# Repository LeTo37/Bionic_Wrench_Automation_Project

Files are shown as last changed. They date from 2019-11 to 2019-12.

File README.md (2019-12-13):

# Part_Placement_Automation_Project
This repository contains the details of my final project for my Masters in Robotics at Northwestern Univeristy. This project entailed the automation of a part of the production process for a specific Wrench and was supervised by Professor Dan Brown.

## Overview
The initial goal of this project was to observe the manufacturing process of the wrench and identify a bottleneck in the process that can be addressed by automation. With that goal set out, there were no set requirements on what should be automated and how it should be automated. This allowed for freedom and trust in following the design process to achieve the optimal solution to this problem.

After journey mapping the manufacturing process, giving time values for each task as well as automatibility ratings and assessments regarding what would be gained from automation, it was clear to see that the set of tasks involved in placing the wrench jaws in the wrench are both the most automatable and automating them will result in the most gain to the entire process. As such the task was set out to use/design whatever is deemed appropriate to automate this process in a way that is both accurate and fast.

The result is shown in the video below:
Mario Kart (https://www.youtube-nocookie.com/embed/1hQX_BQMhLg "Mario Kart")

As will be detailed, the mechanical design for this project was primarily done using <a href="https://www.onshape.com/" target="_blank">OnShape</a> CAD software, the construction of the rig was done using various prototyping methods such as 3D printing and Laser Cutting, a PIC32MX795F512H microcontroller was used to control the system and the relevant peripheral circuitry and coding of the microcontroller was done in C. 

## Approach
As mentioned above, the first step of this project was just to observe. Professor Brown gave me videos of the current production process for the wrench and I began to make note of each task being undertaken, how long each task was taking and how that task affects the other tasks. It was clear that the biggest bottleneck in the process was the placing of the wrench jaws in the wrench. This task represented the biggest gain from automation but also perhaps one of the most challenging steps to automate given the precise needs for placing the jaw as well as the small amount of space in the middle of the wrench in which a mechanism can actuate.

So begun the iterative process of design. The bulk of work done in this project was in mechanical design, each week brought about a new iteration of the current design as well as thoughts on a new approach. That journey can be mapped by following the different "STL" files of the various designs that were cycled through before arriving at the final stop. 

It became important to create journey maps of best case scenarios, so as to assess the approach and figure out what could be done in time as well as what could be done better.
<!-- ![Wrench_Journey_Map](media/Wrench_Journey_Map.pdf) -->
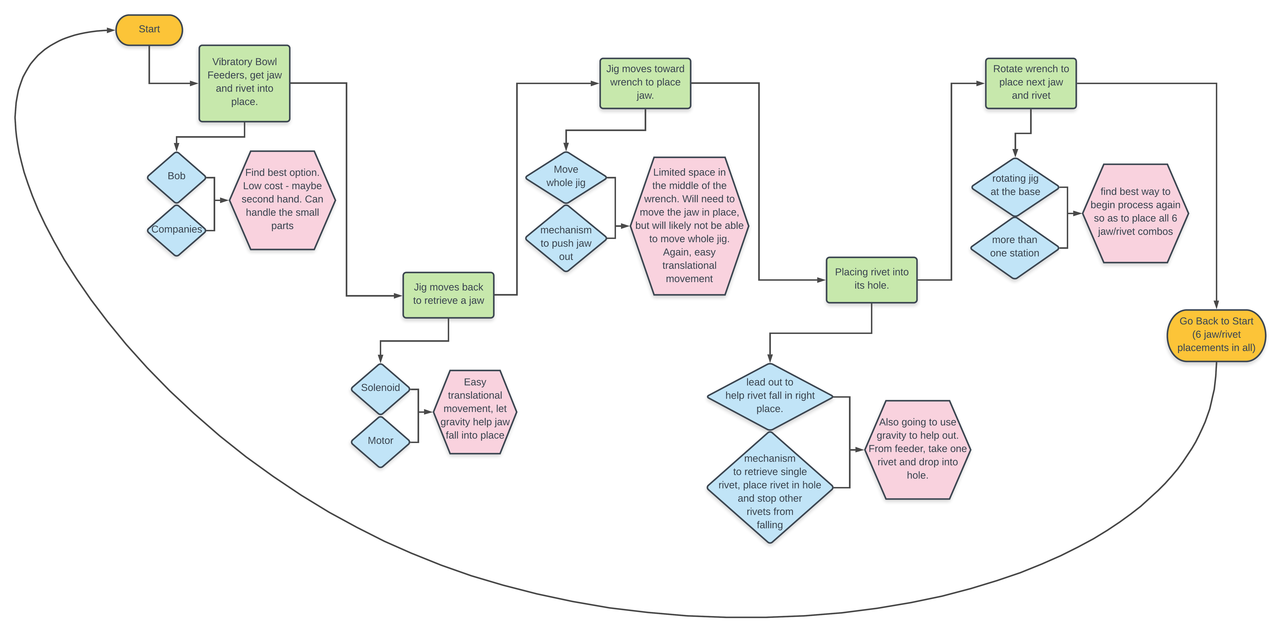
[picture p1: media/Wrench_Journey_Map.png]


A big change in the approach came about when it was decided that using gravity to place the jaws could simplify the process by eliminating the need to actuate within the small space in the middle of the wrench. This came about as a serendipitous thought during a brainstorming session with Professor Brown. 
As such, the final approach was to use gravity to place the jaws in the wrench, with the assistance of an electromagnet and to rotate the wrench around the jig and repeat - so as to place all 6 jaws. This is further detailed in the READMEs of each directory.

## Mechanical Design
The mechanical design involved in this project was by far the most important, most complex and thus the most time consuming aspect of the project. As is the nature of design, it involved a lot of iterations as well as a few changes in approach that ultimately led to the final design. This final set up is shown below.

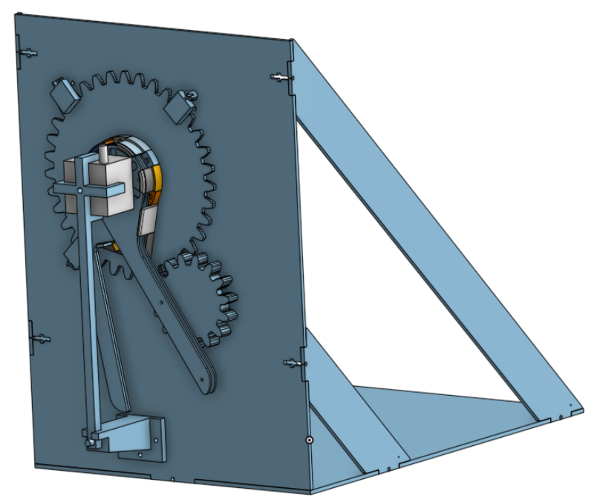
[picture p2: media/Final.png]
Final


The design process is discussed further in the [Mechanical Design Directory](/Mechanical_Design).

## Electronics

[This](/Electronics) directory contains the <a href="https://www.autodesk.com/products/eagle/overview" target="_blank">EAGLE CAD</a> files used to develop the schematics of the circuitry used in this project. It further contains a README explaining the circuitry used.

## Code

The C code used to program the microcontroller is in [this](/Code). directory.

<!-- ## Future Work -->

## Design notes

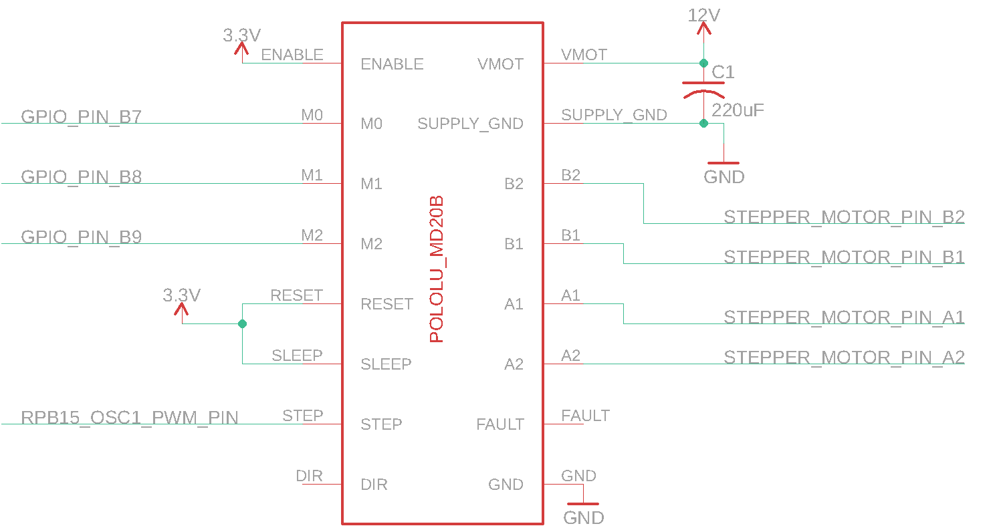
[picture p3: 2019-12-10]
Electronics/STEPPER_MOTOR_DRIVER.png

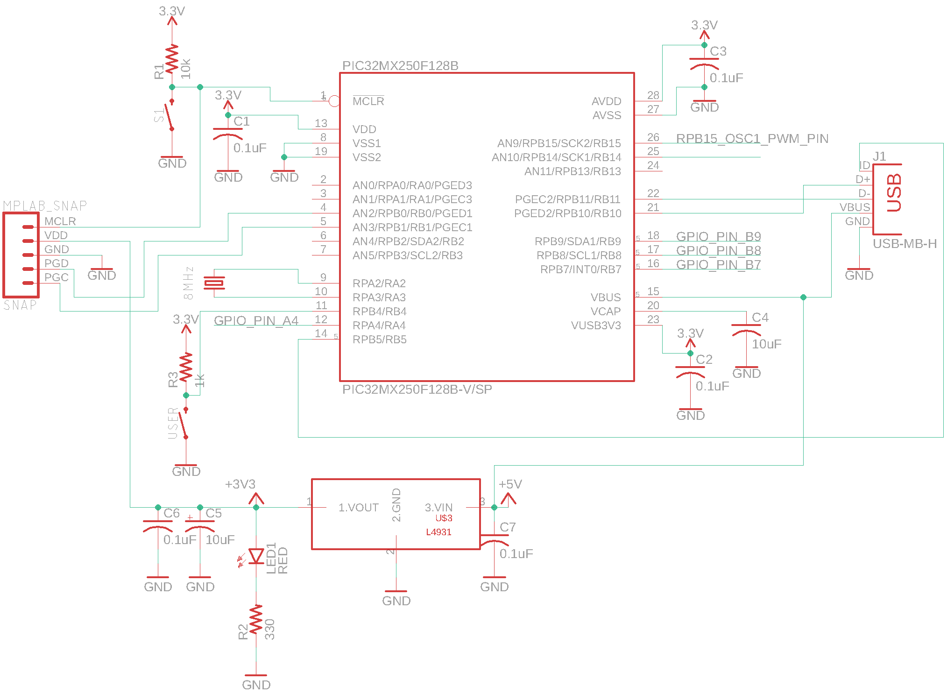
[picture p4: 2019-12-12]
Electronics/PIC32_BREAKOUT.png

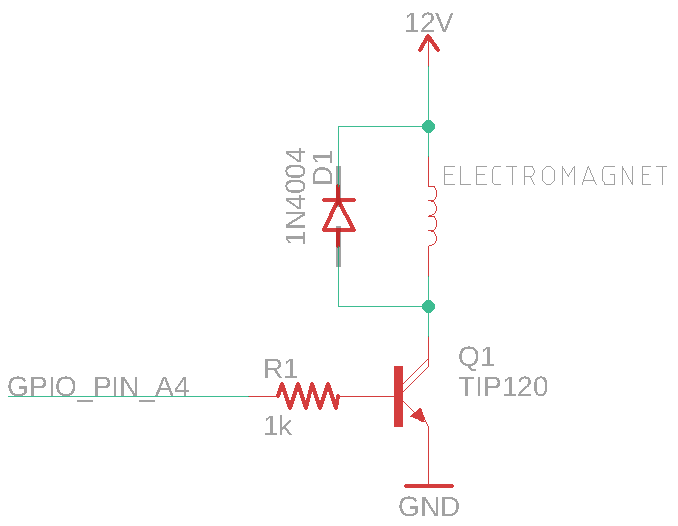
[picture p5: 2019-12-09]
Electronics/ELECTROMAGNET_DRIVER.png

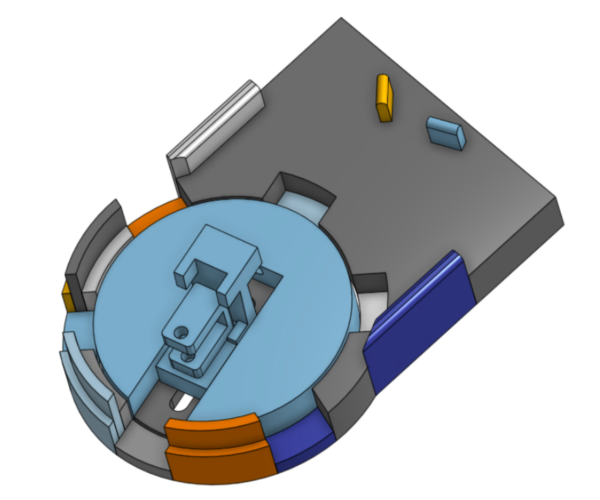
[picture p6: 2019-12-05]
media/Feed_from_top.png

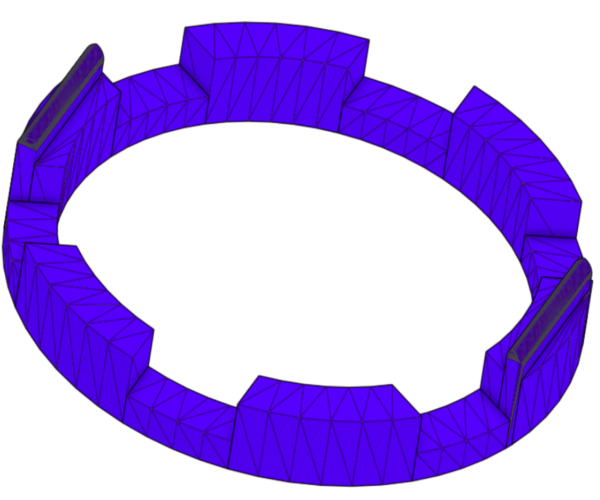
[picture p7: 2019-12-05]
media/wrench_outer_jig_II.png

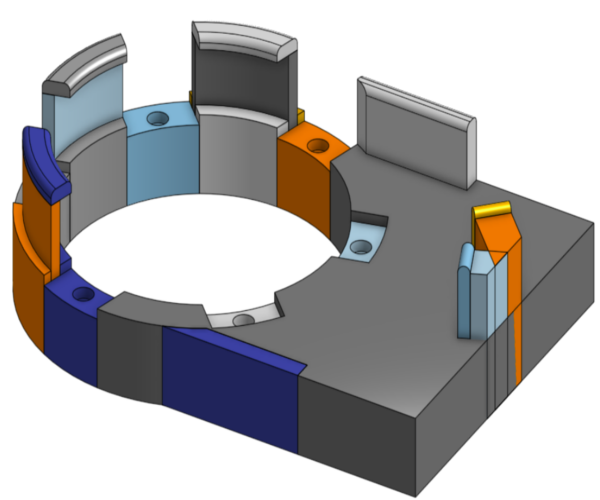
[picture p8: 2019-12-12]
media/jig.png

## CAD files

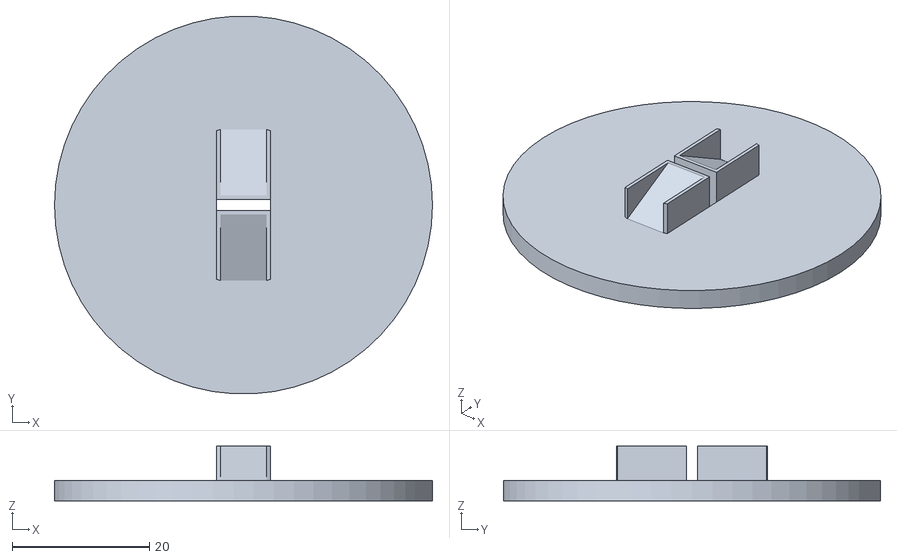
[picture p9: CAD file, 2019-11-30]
Design_Iterations/inside_design_II.stl
55.0 x 54.9 x 8.00

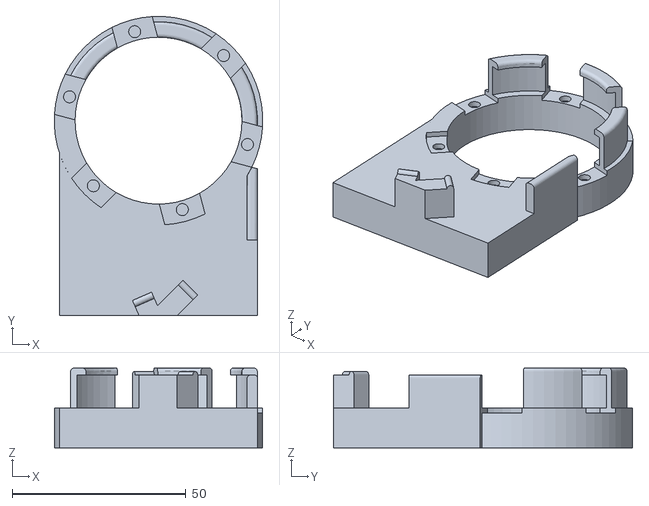
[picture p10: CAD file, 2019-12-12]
Mechanical_Design/Current/3D_Prints/jig.stl
59.9 x 86.0 x 23.0

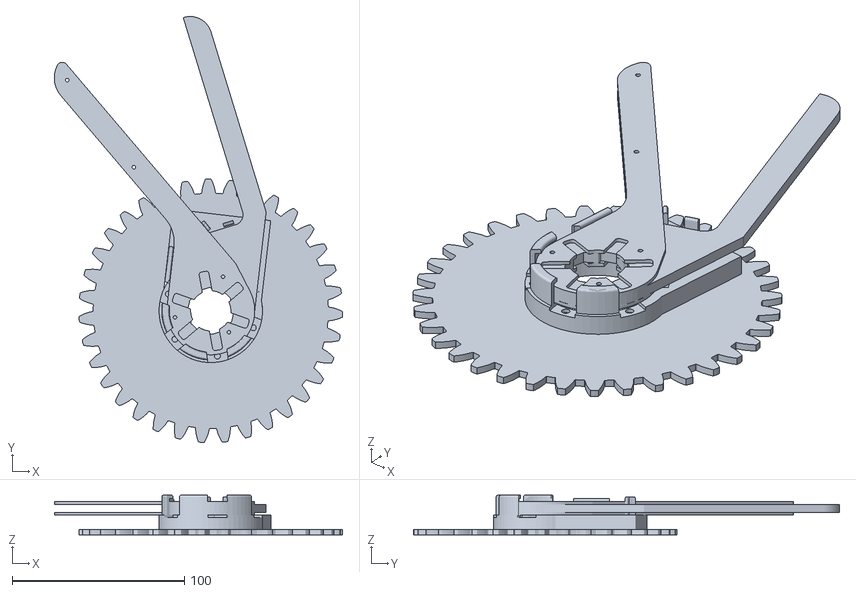
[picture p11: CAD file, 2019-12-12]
Mechanical_Design/Current/Laser_Cut_Pieces/jig_gear.stl
167.3 x 247.2 x 23.0

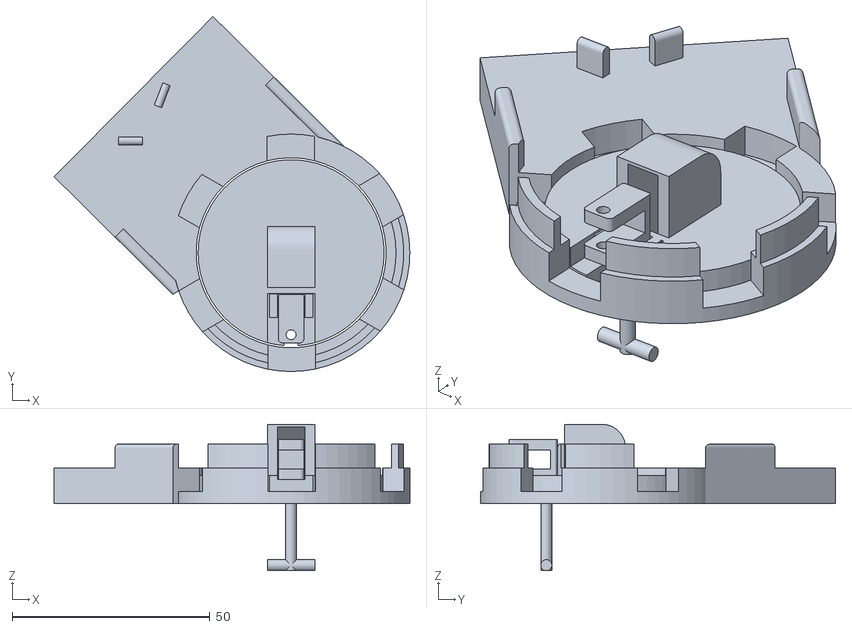
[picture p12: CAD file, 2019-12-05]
Mechanical_Design/Iterations/Feed_from_bottom.stl
89.9 x 89.7 x 37.0

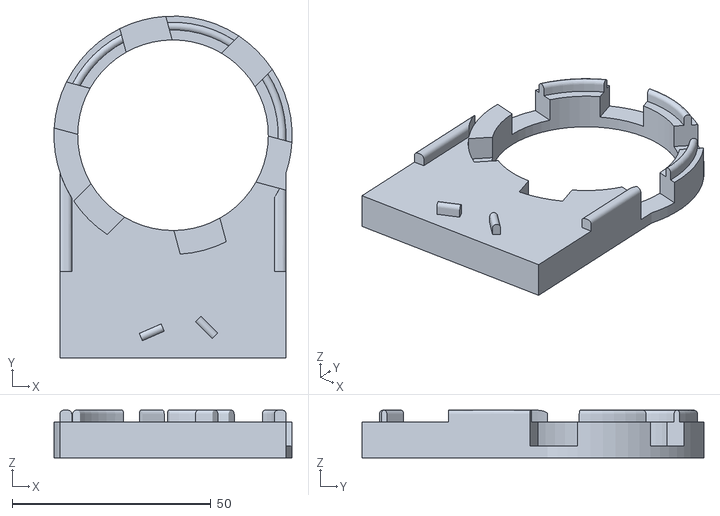
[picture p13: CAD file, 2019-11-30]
Design_Iterations/wrench_outer_jig_IV.stl
59.9 x 86.0 x 12.0

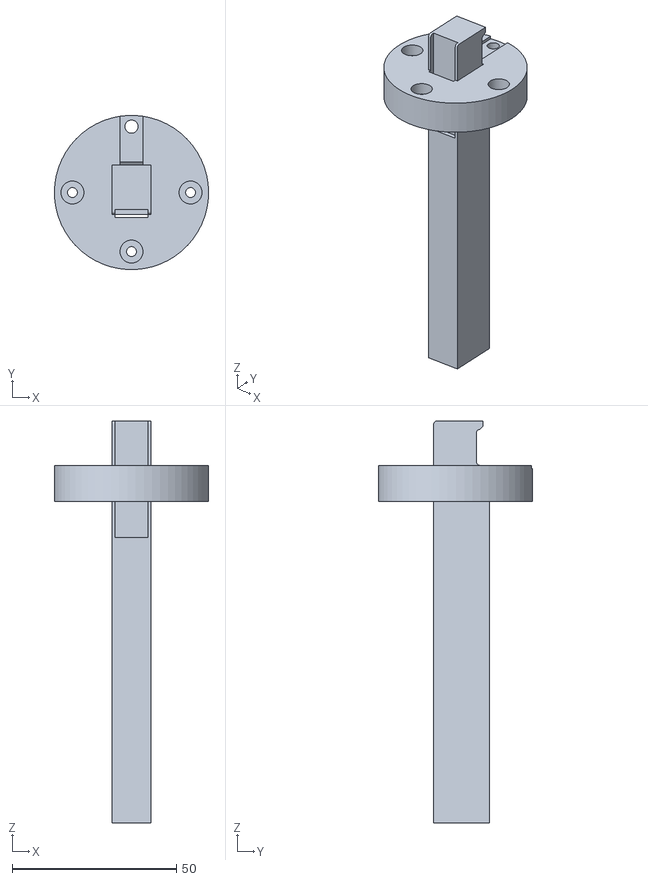
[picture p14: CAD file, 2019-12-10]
Mechanical_Design/Current/3D_Prints/feeder_plus_inner.stl
47.0 x 46.9 x 122.5

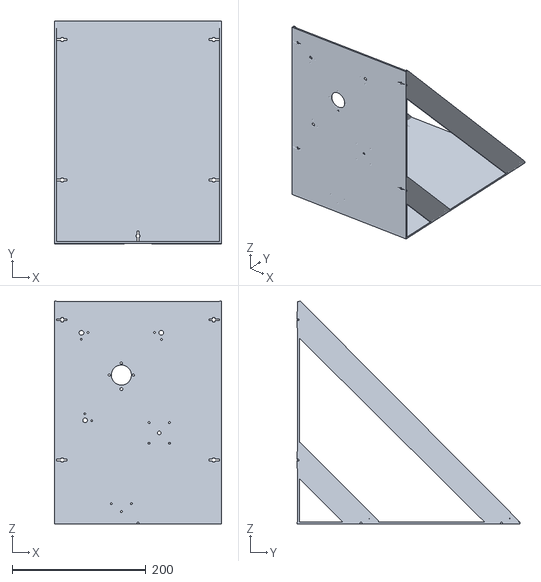
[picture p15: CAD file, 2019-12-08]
Mechanical_Design/Current/Laser_Cut_Pieces/Rig.stl
250.0 x 333.2 x 333.8

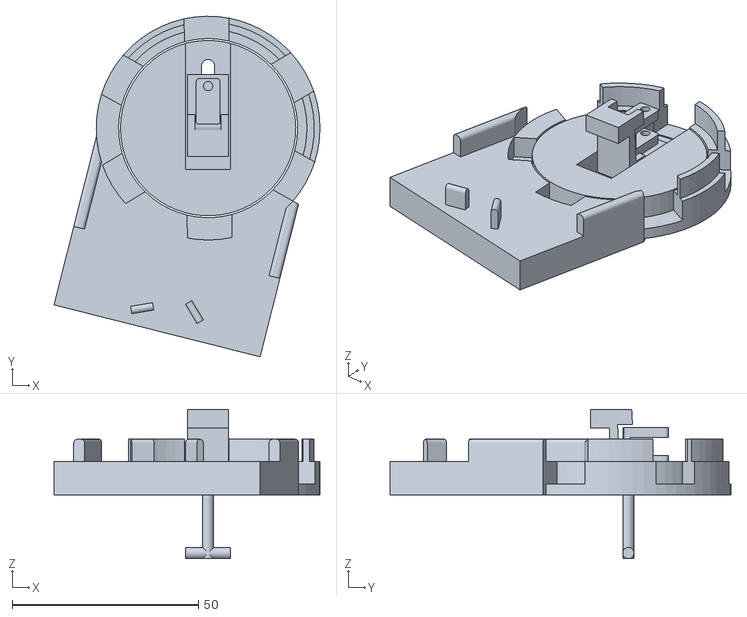
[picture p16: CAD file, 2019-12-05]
Mechanical_Design/Iterations/Feed_from_top.stl
71.3 x 91.3 x 40.0

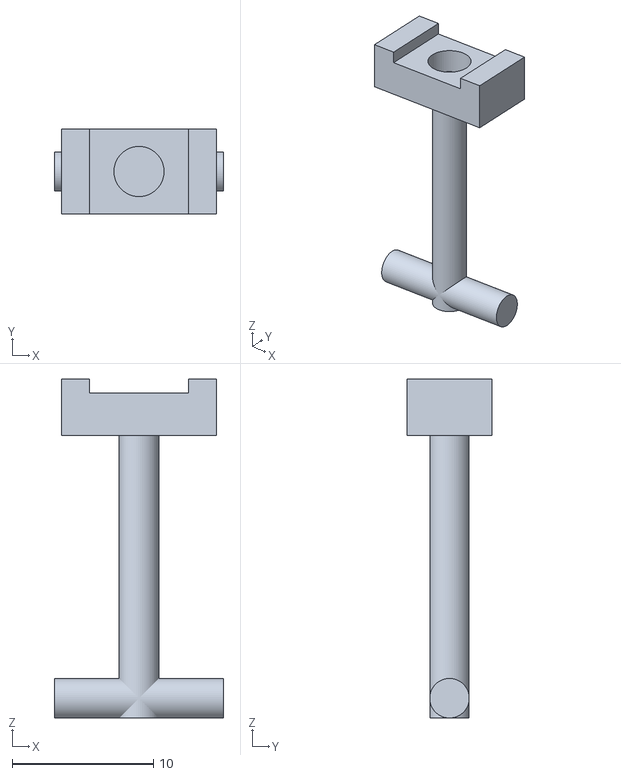
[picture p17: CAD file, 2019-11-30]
Design_Iterations/jaw_pusher_bottom_VII.stl
12.0 x 6.00 x 24.0

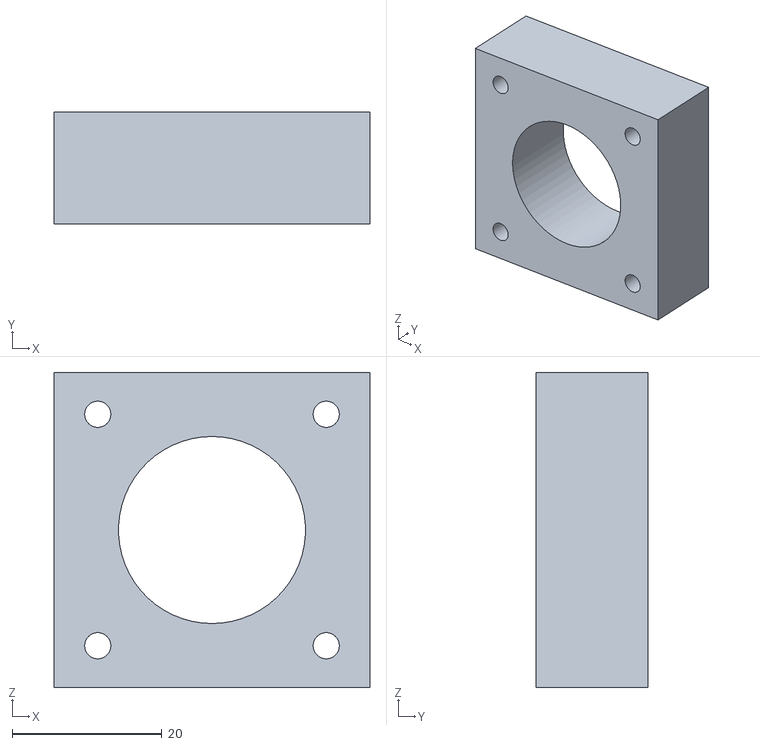
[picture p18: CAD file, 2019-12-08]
Mechanical_Design/Current/3D_Prints/motor_spacer.stl
42.2 x 15.0 x 42.1

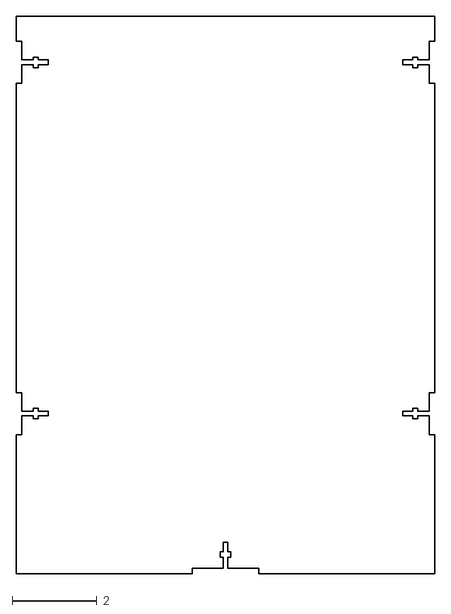
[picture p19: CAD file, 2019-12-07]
Mechanical_Design/Current/Laser_Cut_Pieces/base.dxf
9.84 x 13.1

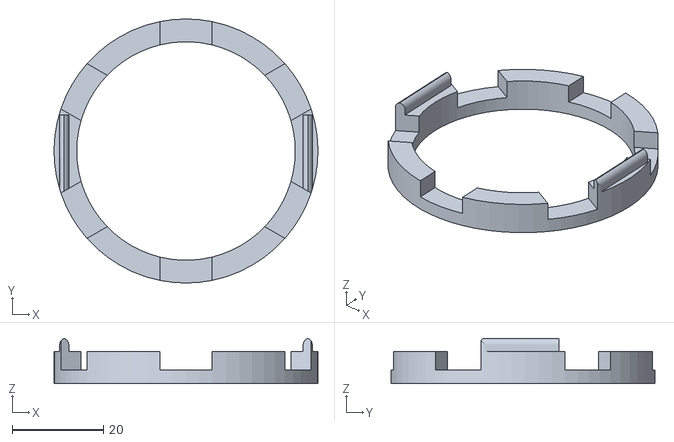
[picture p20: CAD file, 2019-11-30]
Mechanical_Design/Iterations/wrench_outer_jig_II.stl
58.0 x 58.0 x 9.91

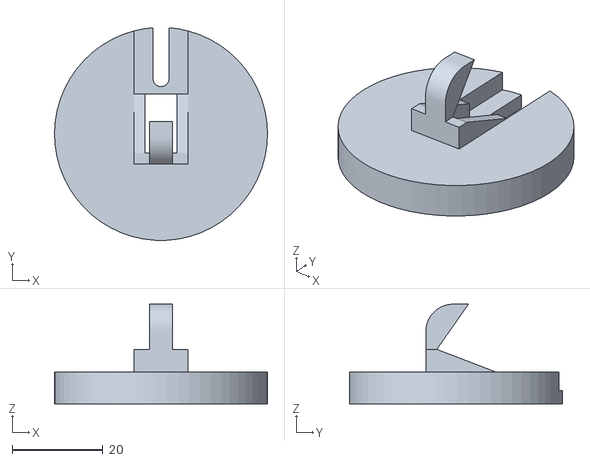
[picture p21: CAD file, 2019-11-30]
Design_Iterations/inner_from_bottom_VI.stl
47.0 x 46.9 x 22.0

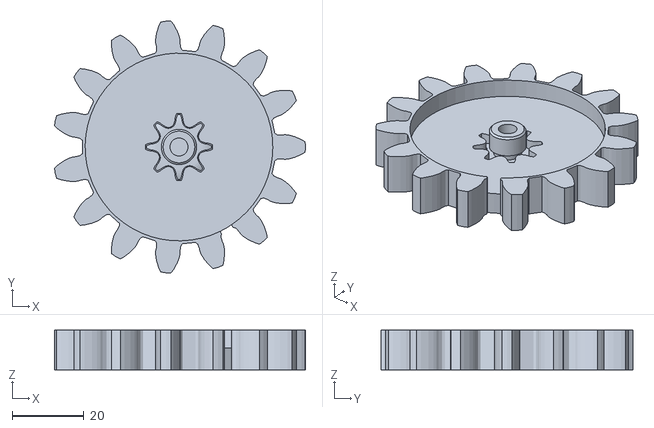
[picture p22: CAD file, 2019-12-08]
Mechanical_Design/Current/3D_Prints/gear_driver.stl
69.8 x 70.1 x 11.0

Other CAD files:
Mechanical_Design/Current/Laser_Cut_Pieces/front.dxf
Mechanical_Design/Iterations/wrench_outer_jig_III.stl
Design_Iterations/inner_from_bottom_V.stl
Mechanical_Design/Current/3D_Prints/clamp.stl
Design_Iterations/inner_from_bottom_IX.stl
Design_Iterations/inner_from_bottom_VIII.stl
Design_Iterations/inside_design_I.stl
Design_Iterations/inside_design_III_a.stl
Design_Iterations/inside_design_III_b.stl
Design_Iterations/jaw_pusher_I.stl
Design_Iterations/jaw_pusher_II.stl
Design_Iterations/jaw_pusher_III.stl
Design_Iterations/jaw_pusher_bottom_V.stl
Design_Iterations/jaw_pusher_bottom_VI.stl
Design_Iterations/jig_VI.stl
Design_Iterations/wrench_inner_jig_I.stl
Design_Iterations/wrench_inner_jig_II.stl
Design_Iterations/wrench_inner_jig_IV.stl
Design_Iterations/wrench_outer_jig_I.stl
Mechanical_Design/Current/3D_Prints/Final.stl
Mechanical_Design/Current/3D_Prints/clamp_1.stl
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

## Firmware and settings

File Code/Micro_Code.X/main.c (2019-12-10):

#include "Setup.h"      //PIC
#include "Stepper.h"    //STEPPER MOTOR
#include"PWM.h"         //PWM

#include <stdio.h>
#include <stdlib.h>
#include <math.h>

int main() {
    __builtin_disable_interrupts();
    // set the CP0 CONFIG register to indicate that kseg0 is cacheable (0x3)
    __builtin_mtc0(_CP0_CONFIG, _CP0_CONFIG_SELECT, 0xa4210583);
    // 0 data RAM access wait states
    BMXCONbits.BMXWSDRM = 0x0;
    // enable multi vector interrupts
    INTCONbits.MVEC = 0x1;
    // disable JTAG to get pins back
    DDPCONbits.JTAGEN = 0;
    //Make B4 an input (USER)
    TRISBbits.TRISB4 = 1;
    //Make A4 an output (ELECMAGNET)
    TRISAbits.TRISA4 = 0;
    //Stepper Motor Setup (and PWM)
    Stepper_Setup();
    PWM_init();
    __builtin_enable_interrupts();

    LATAbits.LATA4 = 1;
    _CP0_SET_COUNT(0);

    //    Step_60();
    int trig = 0;
    int prev = 0;
    while (1) {
        prev = PORTBbits.RB4;
        _CP0_SET_COUNT(0);
        while (_CP0_GET_COUNT() < 24000) {

        }

        if (prev == 1) {
            if (PORTBbits.RB4 == 0) {
                trig++;
            }
        }
        if (trig == 1) {
            LATAbits.LATA4 = 0;
        } else if (trig == 2) {
            LATAbits.LATA4 = 1;
        } else if (trig == 3) {
            Step_60();
            trig = 0;
        }






    }

}

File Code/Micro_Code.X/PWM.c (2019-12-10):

#include"PWM.h"

void PWM_init(void) {
    //Open pins for OC1 and OC2
    RPB15Rbits.RPB15R = 0b0101; //Set B15 as OC1 (PIN 2)

    //***************TIMER 3 PWM********************
    T3CONbits.TCKPS = 0; //Prescaler N=1
    // period = (PR3+1) * N * 20.83 ns
    PR3 = 47999; //With prescaler of 1 give a 1 kHz signal
    TMR3 = 0; //reset the timer  
    T3CONbits.ON = 1; //Turn on the timer
    //********************

    //OC1
    OC1CONbits.OCM = 0b110; //PWM mode without fault pin; other OC1CON bits are defaults
    OC1RS = 0; //0% duty Cycle
    OC1R = 0; //0% duty Cycle
    OC1CONbits.OCTSEL = 1; //Use timer 3
    OC1CONbits.ON = 1; // turn on OC1

}

void setDuty(float percent) //0 = forward, 1 = back
{
    int duty;
    percent = percent / 100;
    duty = (int) (percent * 2400);
    OC1RS = duty;

}

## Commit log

2019-11-30 added a bunch of the design iterations. Write up beginning
    [Assembly_feeder&inner.stl, feeding_tube.stl, inner_from_bottom_IX.stl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]
2019-12-05 Restructure and added README stls
    [Assembly_feeder&inner.stl, Feed_from_bottom.stl, Feed_from_top.stl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]
2019-12-06 Started Code. Restructure repo
    [Assembly_feeder&inner.stl, Feed_from_bottom.stl, Feed_from_top.stl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]
2019-12-06 remove old file
    [Assembly_feeder&inner.stl, Feed_from_bottom.stl, Feed_from_top.stl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]
2019-12-07 Some micro code. Minor Design changes
    [Final.stl, jig.stl]
2019-12-08 Mechanical README
    [Rig.stl, clamp.stl, gear_driver.stl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]
2019-12-09 Electronics README
    [Bionic_Wrench_Electronics.kicad_pcb, Bionic_Wrench_Electronics.sch]
2019-12-09 add '.sch' files
    [Bionic_Wrench_Electronics.kicad_pcb, Bionic_Wrench_Electronics.sch, Electromagnet.sch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]
2019-12-09 README update
    [feeder_plus_inner.stl]
2019-12-10 Code Update. Electronics Update - new driver. README update.
    [feeder_plus_inner.stl]
2019-12-12 electronics update. 3D model update
    [jig.stl, jig_gear.stl]
